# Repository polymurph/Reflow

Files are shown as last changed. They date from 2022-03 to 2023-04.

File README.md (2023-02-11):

# Reflow

## How to Contribute

source: https://www.youtube.com/watch?v=CML6vfKjQss

1. fork the project

2. make a new brachnch in the forked project

3. programm your features

3. one you are done go to your fork on github and hit the "compare & pull request" button

4. describe the feature, adaptation, bugfix or etc.

5. when done with documenting hit the "create pull request" button. 

## README Creation tipps

https://www.youtube.com/watch?v=E6NO0rgFub4

## Git Submodules

source: https://devconnected.com/how-to-add-and-update-git-submodules/

### Adding git submodule¨

-> https://stackoverflow.com/questions/43761594/cmake-and-using-git-submodule-for-dependence-projects

```
git submodule add <remote_url> <destination_folder>
git commit -m "Added the submodule to the project."
git push
```

### update git submodule

```
git submodule update --init --recursive
```

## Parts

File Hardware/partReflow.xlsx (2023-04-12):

DCDC | 24 V to 5 V conversion | TSR 1.5-2450E | Traco | Digikey | 1951-TSR1.5-2450E-ND | 5.4 | USD
LDO | 5V to 3.3 V | LD1117D33TR | STM | Digikey | 497-7306-2-ND | 0.95 | USD
MOTOR Controller | DC moto control lfor Fans | TB6612FNG,C,8,EL | Toshiba (https://www.mouser.ch/manufacturer/toshiba-semiconductors/) | Digikey | TB6612FNGC8ELTR-ND | 1.06 | USD
IO Expader | Digital IO expander for Keypad | PI4IOE5V6416LEX | Diodes | Digikey | PI4IOE5V6416LEXDITR-ND | 1.52 | USD
HHS | High side swith for 24 V user output | VNQ5160K-E | STM | Digikey | 497-19759-ND | 4.6 | USD
Relay Driver | For SoliState Relays 12 or 24 volts. | SZNUD3124DMT1G | OnSemi | Digikey | SZNUD3124DMT1GOSTR-ND | 0.59 | USD
Temperature Sensor | RTD TO DIGITAL CONVERT | MAX31865AAP+T | ADI | Digikey | MAX31865AAP+TTR-ND | 8.02 | USD

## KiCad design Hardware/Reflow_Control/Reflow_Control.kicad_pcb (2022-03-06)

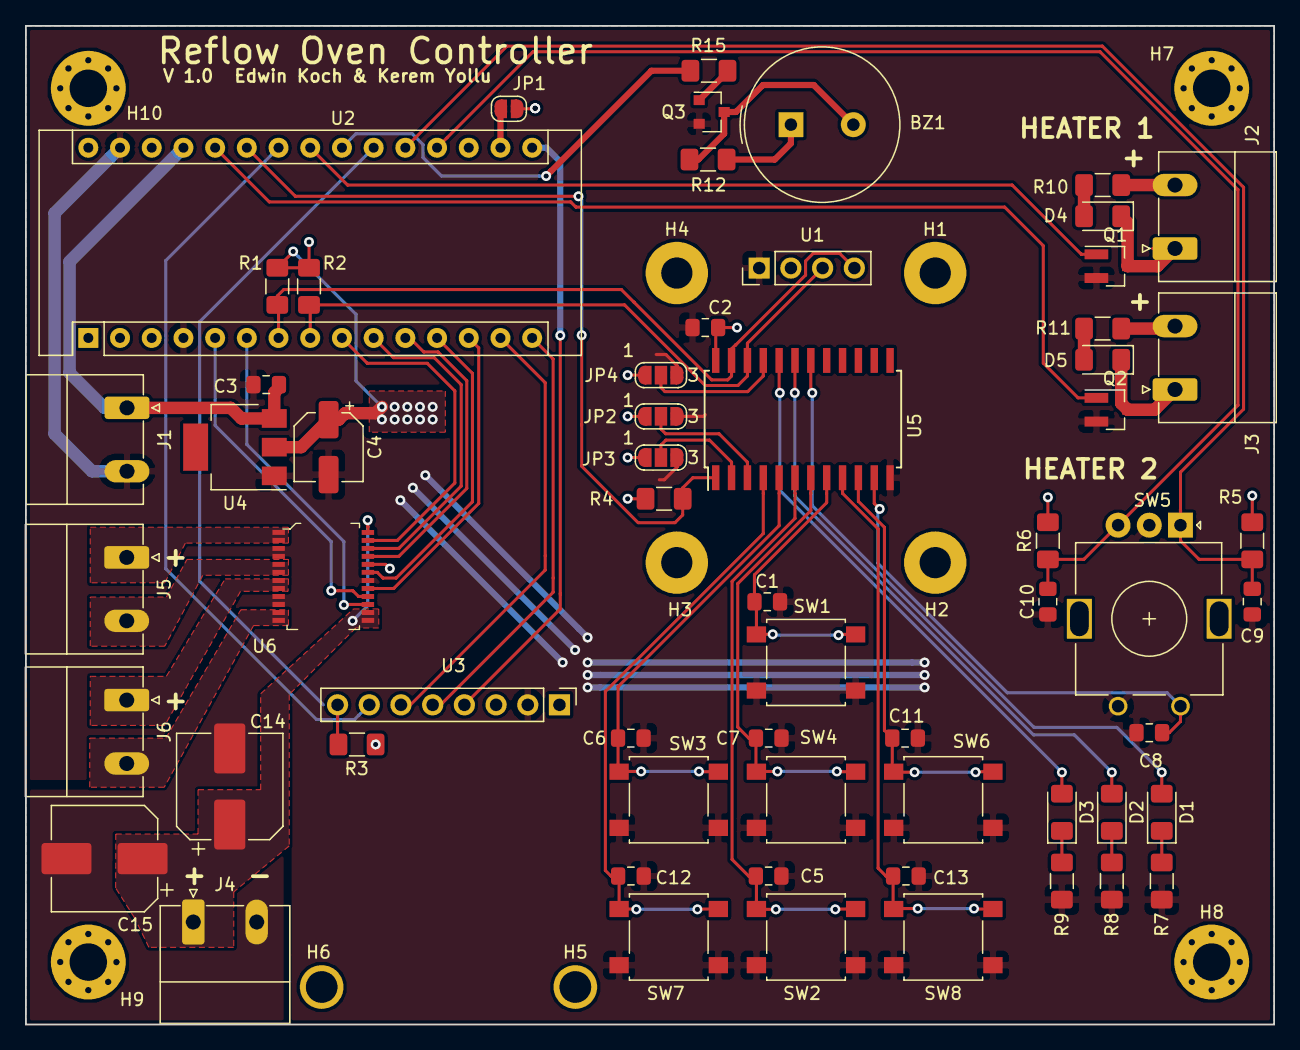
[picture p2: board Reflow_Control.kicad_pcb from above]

Board: 2 copper layers, 100.0 x 80.0 mm, 71 parts (0 on the bottom side), 52 nets.

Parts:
BZ1: Buzzer; Buzzer_TDK_PS1240P02BT_D12.2mm_H6.5mm
C1, C3, C5, C6, C7, C8, C9, C10, C11, C12, C13: 10uF; C_0805_2012Metric_Pad1.15x1.40mm_HandSolder
C2: 100n; C_0805_2012Metric_Pad1.15x1.40mm_HandSolder
C4: 100uF; CP_Elec_5x5.4
C14, C15: 100uF; CP_Elec_8x6.2
D1, D2, D3, D4, D5: LED; LED_1206_3216Metric_Pad1.42x1.75mm_HandSolder
H1, H2, H3, H4, H5, H6: MountingHole; MountingHole_2.5mm_Pad
H7, H8, H9, H10: MountingHole; MountingHole_3mm_Pad_Via
J1: Conn_5V; PhoenixContact_MC_1,5_2-G-5.08_1x02_P5.08mm_Horizontal
J2: Conn_ssr_1; PhoenixContact_MC_1,5_2-G-5.08_1x02_P5.08mm_Horizontal
J3: Conn_ssr_2; PhoenixContact_MC_1,5_2-G-5.08_1x02_P5.08mm_Horizontal
J4: Conn_mot_PWR; PhoenixContact_MC_1,5_2-G-5.08_1x02_P5.08mm_Horizontal
J5: Conn_mot_1; PhoenixContact_MC_1,5_2-G-5.08_1x02_P5.08mm_Horizontal
J6: Conn_mot_2; PhoenixContact_MC_1,5_2-G-5.08_1x02_P5.08mm_Horizontal
JP1: 3.3V Jumper; SolderJumper-2_P1.3mm_Open_RoundedPad1.0x1.5mm
JP2, JP3, JP4: ADDR_A2; SolderJumper-3_P1.3mm_Open_RoundedPad1.0x1.5mm_NumberLabels
Q1: Q_NMOS_GSD; SOT-23_Handsoldering
Q2: NUD3112LT1G; SOT-23_Handsoldering
Q3: BC848; SOT-23
R1, R2, R3, R4, R5, R6, R7, R8, R9: 4k7; R_1206_3216Metric_Pad1.42x1.75mm_HandSolder
R10, R11, R12, R15: 1k; R_1206_3216Metric_Pad1.42x1.75mm_HandSolder
SW1, SW2, SW3, SW4, SW6, SW7, SW8: SW_Push; SW_SPST_B3S-1000
SW5: Rotary_Encoder_Switch; RotaryEncoder_Alps_EC11E_Vertical_H20mm
U1: SSD1306_128x64; PinHeader_1x04_P2.54mm_Vertical
U2: NUCLEO-F042K6; Arduino_Nano
U3: MAX31865_Breakout; PinHeader_1x08_P2.54mm_Vertical
U4: LM1117-3.3; SOT-223
U5: PCA9555; SOIC-24W_7.5x15.4mm_P1.27mm
U6: TB6612FNG_C_8_EL; LSSOP-24_W5.6mm

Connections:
+3V3: BZ1.1, C2.2, C4.1, J2.2, J3.2, JP1.2, JP2.1, JP3.1, JP4.1, R1.1, R2.1, R3.1, R4.1, R5.1, R6.1, R10.1, R11.1, R12.1, U1.2, U3.3, U4.2, U5.24, U6.20
+5V: C3.1, J1.1, U2.27, U4.3
/motor_vcc: C14.1, C15.1, J4.1, U6.13, U6.14, U6.24
ADDR_A0: JP4.2, U5.21
ADDR_A1: JP3.2, U5.2
ADDR_A2: JP2.2, U5.3
BTN_A: C12.1, SW7.1, U5.4
BTN_B: C13.1, SW8.1, U5.9
BTN_CENTER: C7.1, SW4.1, U5.7
BTN_DOWN: C5.1, SW2.1, U5.6
BTN_LEFT: C6.1, SW3.1, U5.5
BTN_RIGHT: C11.1, SW6.1, U5.10
BTN_UP: C1.1, SW1.1, U5.8
CH1_MOTOR_IN1: U2.11, U6.21
CH1_MOTOR_IN2: U2.10, U6.22
CH1_MOTOR_STBY: U2.12, U6.19
CH2_MOTOR_IN1: U2.5, U6.16
CH2_MOTOR_IN2: U2.13, U6.17
ENC_Switch: C8.2, SW5.S1, U5.11
GND: C1.2, C2.1, C3.2, C4.2, C5.2, C6.2, C7.2, C8.1, C9.1, C10.1, C11.2, C12.2, C13.2, C14.2, C15.2, J1.2, J4.2, JP2.3, JP3.3, JP4.3, Q1.2, Q2.2, Q3.2, R7.2, R8.2, R9.2, SW1.2, SW2.2, SW3.2, SW4.2, SW5.C, SW5.S2, SW6.2, SW7.2, SW8.2, U1.1, U2.4, U2.29, U3.2, U4.1, U5.12, U6.3, U6.4, U6.9, U6.10, U6.18
I2C1_SCL: R2.2, U1.3, U2.8, U5.22
I2C1_SDA: R1.2, U1.4, U2.7, U5.23
INT_ENC_A: C10.2, R6.2, SW5.B, U2.19
INT_ENC_B: C9.2, R5.2, SW5.A, U2.20
INT_MAX31865_RDY: R3.2, U2.21, U3.8
INT_PCA9555: R4.2, U2.25, U5.1
unnamed: BZ1.2, Q3.3, R12.2
unnamed: D1.1, R7.1
unnamed: D1.2, U5.18
unnamed: D2.1, R8.1
unnamed: D2.2, U5.19
unnamed: D3.1, R9.1
unnamed: D3.2, U5.20
unnamed: D4.1, J2.1, Q1.3
unnamed: D4.2, R10.2
unnamed: D5.1, J3.1, Q2.3
unnamed: D5.2, R11.2
unnamed: J5.1, U6.1, U6.2
unnamed: J5.2, U6.5, U6.6
unnamed: J6.1, U6.7, U6.8
unnamed: J6.2, U6.11, U6.12
unnamed: JP1.1, U2.17
unnamed: Q3.1, R15.1
SPI1_CS_MAX31865: U2.24, U3.7
SPI1_MISO: U2.15, U3.5
SPI1_MOSI: U2.14, U3.6
SPI1_SCK: U2.16, U3.4
SSR_1: Q1.1, U2.23
SSR_2: Q2.1, U2.26
TIM1_CH1_PWM_Buzzer: R15.2, U2.22
TIM3_CH1_MOTOR_PWM: U2.9, U6.23
TIM3_CH2_MOTOR_PWM: U2.6, U6.15

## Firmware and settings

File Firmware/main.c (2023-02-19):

#include "main.h"
#include "reflow_oven_bsl.h"
#include "ovenCtrl.h"

#ifdef TO_BE_DISCUSSED
#include "bsl_config.h"
#endif

int main(int argc, char *argv[])
{
	uint8_t i = 0;

	// creating ovenBSL object
	reflowBSL_t ovenBSL; 

	// init of ovenBSL object
	ovenBSL.clockSpeed=8000000; 
	ovenBSL.statusLED=pinB3; 
	ovenBSL.resetPin=pinA0;
	ovenBSL.uartTx=pinA2;
	ovenBSL.uartRx=pinA15;
	ovenBSL.uartChannel=usart2; 
	ovenBSL.baudRate=115200;

	// init reflow oven controller
	ovenCtrl_init(&ovenBSL);
	
	// run reflow oven  controller
	ovenCtrl_run();	

	while(1);

	return 1;
}

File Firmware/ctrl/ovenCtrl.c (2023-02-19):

#include "ovenCtrl.h"
#include "oven.h"
#include "modules.h"
#include "deviceSetup.h"

typedef enum {
    st_idle,
    st_rampToSoak,
    st_soak,
    st_rampToPeak,
    st_dwell,
    st_coolDown
}state_t;

static state_t currentState = st_idle;


// reflow parameters
static float T_base = 0.0;
static float t_rampToSoak = 0;
static float T_soakStart = 0.0;
static float t_soak = 0;
static float T_soakEnd = 0.0;
static float t_rampToPeak = 0;
static float T_peak = 0.0;
static float t_dwell = 0;
static float t_coolDown = 0;

// precalculated parameters
static float m_rampToSoak = 0.0;
static float m_soak = 0.0;
static float m_rampToPeak = 0.0;
static float m_coolDown = 0.0;


//
static float reflowTimer = 0.0;
static float timerPeriode = 0.0;

void _abort()
{
    print_Usart(oven_bsl->uartChannel, "Process Aborted!\n");
    oven_turnOffHeater();
    print_Usart(oven_bsl->uartChannel, "Changing to State: st_rampToSoak\n");
    currentState = st_coolDown;
}

void ovenCtrl_init(reflowBSL_t* bsl)
{
    currentState = st_idle;
	// init board suport layer (BSL)
	reflowOvenInitHw(bsl);
	// init reflow oven (ui, timer, etc.)
    
    //oven_init();
    reflowTimer = 0.0;

    setupInit();

    // init done!indicate by toggling LED
	userIO_doInitStatusBlinki();
}

void ovenCtrl_handleEvent(oven_event_t event)
{
    switch(currentState) {
        case st_idle:
            print_Usart(oven_bsl->uartChannel, "State: st_idle\n");
            if(event == ev_start) {
                oven_turnOnHeater();
                print_Usart(oven_bsl->uartChannel, "Changing to State: st_rampToSoak\n");
                currentState = st_rampToSoak;
            }
            break;

        case st_rampToSoak:
            print_Usart(oven_bsl->uartChannel, "State: st_rampToSoak\n");
            if(event == ev_abort) {
                _abort();
                break;
            } else if (event == ev_soakTempReaced) {
                print_Usart(oven_bsl->uartChannel, "Changing to State: st_Soak\n");
                currentState = st_soak;
                break;
            }
            break;

        case st_soak:
            print_Usart(oven_bsl->uartChannel, "State: st_soak\n");
            if(event == ev_abort) {
                _abort();
                break;
            } else if (event == ev_soakDone) {
                print_Usart(oven_bsl->uartChannel, "Changing to State: st_rampToPeak\n");
                currentState = st_rampToPeak;
            }
            break;

        case st_rampToPeak:
            print_Usart(oven_bsl->uartChannel, "State: st_rampToPeak\n");
            if(event == ev_abort) {
                _abort();
                break;
            } else if (event == ev_peakTempReached) {
                print_Usart(oven_bsl->uartChannel, "Changing to State: st_dwell\n");
                currentState = st_dwell;
            }
            break;

        case st_dwell:
            print_Usart(oven_bsl->uartChannel, "State: st_dwell\n");
            if(event == ev_abort) {
                _abort();
                break;
            } else if (event == ev_dwellTimeOver) {
                print_Usart(oven_bsl->uartChannel, "Changing to State: st_coolDown\n");
                currentState = st_coolDown;
            }
            break;

        case st_coolDown:
            print_Usart(oven_bsl->uartChannel, "State: st_coolDown\n");
            if(event == ev_ovenCooledDown) {
                print_Usart(oven_bsl->uartChannel, "Changing to State: st_idle\n");
                oven_turnOffHeater();
                currentState = st_idle;
            }
            break;

        default:
            print_Usart(oven_bsl->uartChannel, "Illegal state!\n");
            break;
    }
}

void ovenCtrl_run()
{
	while(1) {
	
	}
}


#ifdef IDEAS

float ovenCtrl_getTempSetValue(float T)
{
    float setTemp;

    switch(currentState) {

        case st_rampToSoak:
            if(T >= T_soakStart) {
                ovenCtrl_handleEvent(ev_soakTempReaced);
                reflowTimer = 0.0;
                return T_soakStart;
            }
            // wait until base temperature is reached
            if(T < T_base) {
                return T_base;
            }
            setTemp =  m_rampToSoak * reflowTimer + T_base;
            break;

        case st_soak:
            if(T >= T_soakEnd) {
                ovenCtrl_handleEvent(ev_soakDone);
                reflowTimer = 0.0;
                return T_soakEnd;
            }
            setTemp = m_soak * reflowTimer + T_soakStart;
            break;

        case st_rampToPeak:
            if(T >= T_soakEnd) {
                ovenCtrl_handleEvent(ev_soakDone);
                reflowTimer = 0.0;
                return T_peak;
            }
            setTemp = m_rampToPeak * reflowTimer + T_soakEnd;
            break;

        case st_dwell:
            if(reflowTimer > t_dwell) {
                ovenCtrl_handleEvent(ev_dwellTimeOver);
                reflowTimer = 0.0;
                return T_peak;
            }
            setTemp = T_peak;
            break;

        case st_coolDown:
            if(T < T_base) {
                ovenCtrl_handleEvent(ev_dwellTimeOver);
                reflowTimer = 0.0;
                return T_base;
            }
            setTemp = m_coolDown * reflowTimer + T_peak;
            break;

        default:
            break;
    }
    // count time
    reflowTimer += timerPeriode;
    return setTemp;
}


void ovenCtrl_controllLoop()
{
    float T_error;
    float T_set;
    float T_measured;
    float u;
    // read temp
    // set set temperature according to ovenCtrl_getTempSetValue()

    // calculate error
    error = T_set - T_measured;

    // run PI controller

    oven_setDutycycle(u);
}
#endif // IDEAS

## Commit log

2022-03-06 added reflow pcb project v1.0
    [Reflow_Control-B.Cu.gbr, Reflow_Control-B.Mask.gbr, Reflow_Control-B.Paste.gbr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]
2022-12-31 working on the temperature controller
2023-02-11 Declared the oven object (typedef struct) and used it to init the board
2023-02-19 added PID class
2023-04-09 created new reflow HW platform + started with block circuit
    [PSU.kicad_sch, ReflowController.kicad_pcb, ReflowController.kicad_sch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]
2023-04-10 work on uC
    [PSU.kicad_sch, ReflowController.kicad_sch, uC.kicad_sch]
2023-04-12 defined rough structure with kerem
    [IO.kicad_sch, PSU.kicad_sch, ReflowController.kicad_sch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]
2023-04-12 started with schematic
    [ReflowController.kicad_sch, TemperatureReader.kicad_sch]
2023-04-13 IMplemented the relay driver and High side switch. For the HSS there are some values to be caculated to enhance safety measures if we decide to implment them
    [IO.kicad_sch, ReflowController.kicad_sch]
2023-04-13 work on temp ic circuit
    [ReflowController.kicad_sch, TemperatureReader.kicad_sch]
2023-04-13 Chnaged fan conroller
    [fanDriver.kicad_sch]
2023-04-14 Finished the fan controllers calculations, added the wago connectors, added notes
    [IO.kicad_sch, PSU.kicad_sch, ReflowController.kicad_sch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]
2023-04-14 Added the IO expander and RJ45 Connectors for LCD and Keypad Connectors
    [ReflowController.kicad_sch, ui.kicad_sch]
2023-04-15 work on MAX31865 circuit
    [TemperatureReader.kicad_sch]
2023-04-15 work on schematic
    [ReflowController.kicad_sch]
2023-04-15 work on circuit
    [ReflowController.kicad_sch]
2023-04-15 updated main schematic with kerem
    [ReflowController.kicad_sch, ui.kicad_sch]
